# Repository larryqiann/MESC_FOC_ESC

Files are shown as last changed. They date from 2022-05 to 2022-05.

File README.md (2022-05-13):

# MESC_FOC_ESC
MESC, Molony ESC, STM32F303 based FOC+BLDC ready, HALL, Encoder, Sensorless, single sides, 2 layer, ~90A @48V

This ESC is intended as a cost optimised alternative to the VESC, by utilising:

Standalone, industry standard footprint gate drivers

Standard D2PAK or H2PAK FETs

Cheap (~2.5$) STM32F303CB microcontroller

Board dimensions 100mmx50mm, so that it can be panelised and manufactured by JLCPCB, or two boards can be combined into one 100mm2 JLCPCB

It is not cross compatible with VESC software, and does not intend to be. VESC has run away with itself in terms of cost, firmware abstraction... in the opinion of this project's author.

# Current Status:  

## Changes made by larryqiann:
Change power architecture to use MP9486A to create 12V rail, from  which 3.3V and 5V will be regulated to reduce quiescent power draw

Add CAN bus transceiver to support CAN bus integration because F303CB supports CAN2.0b

## Previous:

First build has been made. All functions... function.
Photos in folder! Video of prelim run to be added to Youtube.
Step down works
Step up for Gate drives works
Chip works, all inputs and outputs works
Some concerns about stability of internal opamps... Returning 1.5V instead of 1.6V. First chip soldered returned 1V, and fluctuated by +0.3/-0.1V. 
Motor spins in BLDC mode (6 step) with hall sensors, on Propdrive 2826 1200kV and with APS8072 50kV. Current run up to 20A phase, with minimal PCB heating with no heatsink. Only run to 23V so far, owing to PSU limitation.
FET switching time rather slow with 5 ohm resistors, limiting peak current to 2A (not counting FET and Gate drive resistance) will reduce to 2R7.

# Layout:  
Layout optimised to minimise current loop path, and keep the board completely single sided assembly.

For thermal management, the FETs have vias underneath the drains, which can be interfaced with a heatsink on the PCB underside, using silicone pad/thermal paste & insulator.

# MCU uses:
Timer1 on PA8,9,10 (high) and PB13,14,15 for PWM generation.

Onboard opamps for current sensing and paralelled comparators input on pins PA1,7, PB0.

Phase voltages can be measured on PA3,4,5, or alternatively, digitally read to detect ZC .

Main voltage can be read on PA0.

# Interfaces:
External Interfaces include Hall/Encoder, I2C, PWM in, UART, USB FS.

Hall sensors on Timer4 PB6,7,8, alternatively Encoder can be run on Tim4 PB6,7

Timer3 channel 1 for standard RC PWM input.

USART3 Tx Rx on PB10,11.
USB on PA11,12, with 1k5 pullup to signal FS mode. Canbe used for reflashing (hypothetically).

I2C1 on PA15(SCL) and PB9(SDA), with a plug for a standard SSD1306 breakout. Alternatively, inertial sensor board could be plugged on breakout wire.

Expected BoM cost:  
0.4USD board  
6x2USD FETs  
2.5USD MCU  
3x1USD gate drives  
1USD SMPS converter  
0.4USD inductor  
??? connector cost (dependent on what's fitted, wire in...)  
0.3USD linear reg  
~3USD caps (dependent on how many you want to solder on, which is dependent on distance to battery, desire to comply with EMC, headroom above FET voltage... etc.)  
0.6USD shunts and other resistors  
0.3USD Optional TVS diode, primarily to protect SMPS, which is only rated to 65V  
Total: ~23-24USD

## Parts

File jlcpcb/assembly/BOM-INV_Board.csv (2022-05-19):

Comment | Designator | Footprint | LCSC
AO3401A | Q2 | SOT-23 | C15127
C_10pF | C22,C31 | C_0603_1608Metric | C1634
C_5.1nF | C24,C33 | C_0603_1608Metric | C53987
STM32F303CBTx | U1 | LQFP-48_7x7mm_P0.5mm | C108516
D_Zener_3v3 | D11,D13,D9 | D_MiniMELF | C145245
C_100nF_16V | C25,C37,C5,C8 | C_0603_1608Metric | C14663
C_100pF_16V | C16,C19,C20,C29 | C_0603_1608Metric | C14858
L_47uH_2.0A | L1 | L_Bourns_SRP7028A_7.3x6.6mm | C149588
D_Sch_100V_2A | D14,D4,D8 | D_SOD-123F | C14996
R_82k | R1,R37,R42,R58,R65 | R_0603_1608Metric | C17840
L_15uH_3A | L2,L3 | L_Bourns_SRP7028A_7.3x6.6mm | C182182
INA181 | U4,U6,U7 | SOT-23-6 | C2058943
R_100 | R13,R14 | R_0603_1608Metric | C22775
R_150 | R19,R26,R34 | R_0603_1608Metric | C22808
R_1.5k | R10,R12,R20,R21,R22,R25,R27,R36,R41,R5,R51,R66 | R_0603_1608Metric | C22843
LED_Small | D3 | LED_0603_1608Metric | C2286
R_1.96K | R44 | R_0603_1608Metric | C22975
R_3.24K | R29 | R_0603_1608Metric | C22978
R_30K | R17,R18,R23,R24,R31,R32 | R_0603_1608Metric | C22984
R_4k7 | R11,R15,R2,R30,R33,R4,R6,R7 | R_0603_1608Metric | C23162
R_5 | R38,R39,R40,R45,R46,R47,R48,R49,R50 | R_0603_1608Metric | C23164
R_5.76K | R16,R35 | R_0603_1608Metric | C23189
R_590K | R3 | R_0603_1608Metric | C23203
R_10.2K | R28,R43 | R_0603_1608Metric | C25804
Shunt | R52,R53,R54,R55,R56,R57 | R_2512_6332Metric | C270947
D_Zener_16V | D20,D21,D22,D23,D24,D25 | D_SOD-123 | C27754
C_8.2nF | C21,C30 | C_0603_1608Metric | C27920
C_0.1uF_100V | C1,C10,C17,C4,C52,C68,C7,C71,C9 | C_0603_1608Metric | C28233
IR2181 | U10,U11,U9 | SOIC-8_3.9x4.9mm_P1.27mm | C380794
CRSS037N10N | Q3,Q4,Q5,Q6,Q7,Q8 | TO-263-2 | C455308
C_4.7nF | C11,C12 | C_0603_1608Metric | C53987
D_Sch_100V_2A | D15,D16,D17 | D_SOD-123F | C64898
C_2.2uF 100V | C2,C3 | C_1206_3216Metric | C650969
ASE-xxxMHz | X1 | X1OSC | C70556
C_100uF_25V | C18 | CP_Elec_6.3x7.7 | C72477
D_Zener_3V3 | D19,D26 | D_MiniMELF | C8056
2N7002 | Q1 | SOT-23 | C8545
C_1uF_100V | C34,C35,C36,C38,C39,C40,C47,C48,C50,C51,C53,C54,C55,C56,C57,C58,C59,C6,C60,C61,C62,C64,C67,C69,C70,C72,C73,C74 | C_0603_1608Metric | C91151
Thermistor_NTC | TH1 | R_0603_1608Metric | C92367
C_10uF_25V | C13,C23,C26,C27,C28,C32,C43,C44,C45 | C_0603_1608Metric | C96446
TPS54331DR | U5,U8 | SOIC-8-1EP_3.9x4.9mm_P1.27mm_EP2.29x3mm_ThermalVias | C9865
Conn_01x08_Female | J6 | JST_PH_B8B-PH-K_1x08_P2.00mm_Vertical
SMF05CT1G | U14 | SOT-363_SC-70-6
MP9486A | U3 | SOIC-8-1EP_3.9x4.9mm_P1.27mm_EP2.41x3.3mm_ThermalVias
TJA1051T | U2 | SOIC-8_3.9x4.9mm_P1.27mm
SMF05CT1G | U12 | SOT-363_SC-70-6
SMF05CT1G | U13 | SOT-363_SC-70-6
Conn_01x08_Female | J5 | JST_PH_B8B-PH-K_1x08_P2.00mm_Vertical
CP_470uF+ | C46 | CP_Radial_D16.0mm_P7.50mm
Conn_01x02_Male | J8 | XT60
Conn_01x06_Male | J3 | PinHeader_1x06_P2.54mm_Vertical
Conn_01x06_Female | J4 | JST_PH_B6B-PH-K_1x06_P2.00mm_Vertical
CP_470uF+ | C42 | CP_Radial_D16.0mm_P7.50mm
CP_470uF+ | C41 | CP_Radial_D16.0mm_P7.50mm
Conn_01x05_Male | J7 | JST_PH_B5B-PH-K_1x05_P2.00mm_Vertical

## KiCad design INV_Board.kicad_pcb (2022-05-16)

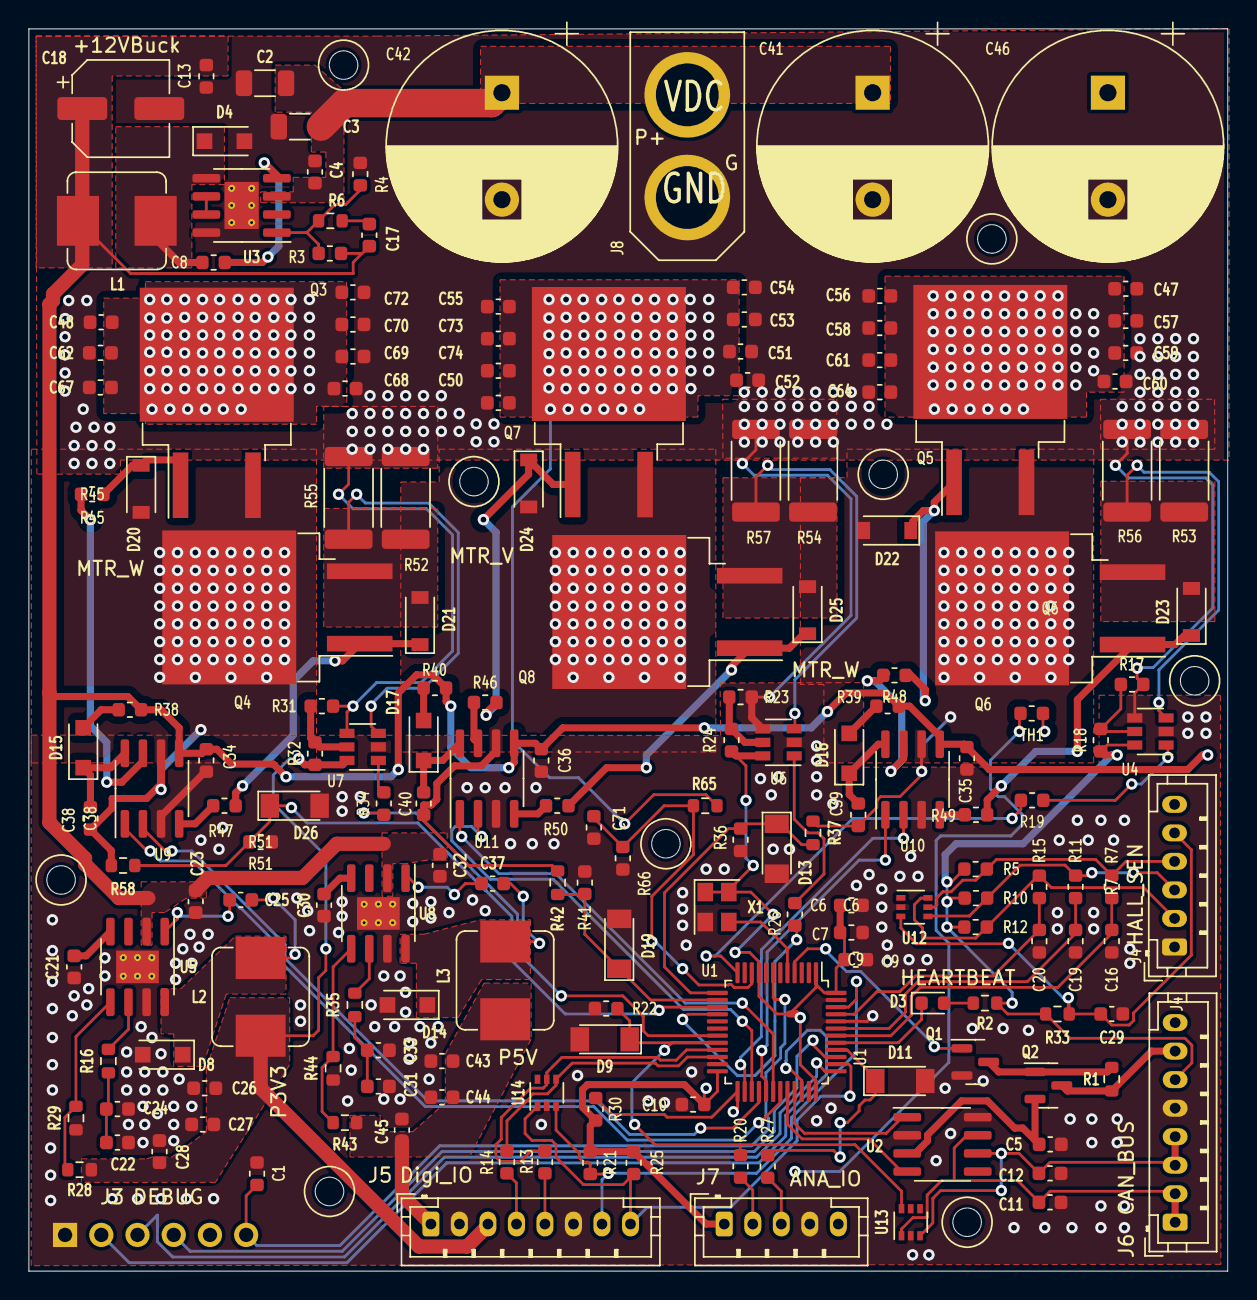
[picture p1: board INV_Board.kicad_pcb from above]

Board: 4 copper layers, 84.1 x 87.1 mm, 177 parts (1 on the bottom side), 97 nets.

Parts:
C1, C4, C7, C9, C10, C17, C52, C68, C71: C_0.1uF_100V; C_0603_1608Metric
C2, C3: C_2.2uF 100V; C_1206_3216Metric
C5, C8, C25, C37: C_100nF_16V; C_0603_1608Metric
C6, C34, C35, C36, C38, C39, C40, C47, C48, C50, C51, C53, C54, C55, C56, C57, C58, C59, C60, C61, C62, C64, C67, C69, C70, C72, C73, C74: C_1uF_100V; C_0603_1608Metric
C11, C12: C_4.7nF; C_0603_1608Metric
C13, C23, C26, C27, C28, C32, C43, C44, C45: C_10uF_25V; C_0603_1608Metric
C16, C19, C20, C29: C_100pF_16V; C_0603_1608Metric
C18: C_100uF_25V; CP_Elec_6.3x7.7
C21, C30: C_8.2nF; C_0603_1608Metric
C22, C31: C_10pF; C_0603_1608Metric
C24, C33: C_5.1nF; C_0603_1608Metric
C41, C42, C46: CP_470uF+; CP_Radial_D16.0mm_P7.50mm
D3: LED_Small; LED_0603_1608Metric
D4, D8, D14, D15, D16, D17: D_Sch_100V_2A; D_SOD-123F
D9, D11, D13: D_Zener_3v3; D_MiniMELF
D19, D26: D_Zener_3V3; D_MiniMELF
D20, D21, D22, D23, D24, D25: D_Zener_16V; D_SOD-123
J3: Conn_01x06_Male; PinHeader_1x06_P2.54mm_Vertical
J4: Conn_01x06_Female; JST_PH_B6B-PH-K_1x06_P2.00mm_Vertical
J5, J6: Conn_01x08_Female; JST_PH_B8B-PH-K_1x08_P2.00mm_Vertical
J7: Conn_01x05_Male; JST_PH_B5B-PH-K_1x05_P2.00mm_Vertical
J8: Conn_01x02_Male; XT60
L1: L_47uH_2.0A; L_Bourns_SRP7028A_7.3x6.6mm
L2, L3: L_15uH_3A; L_Bourns_SRP7028A_7.3x6.6mm
Q1: 2N7002; SOT-23
Q2: AO3401A; SOT-23
Q3, Q4, Q5, Q6, Q7, Q8: CRSS037N10N; TO-263-2
R1, R37, R42, R58, R65: R_82k; R_0603_1608Metric
R2, R4, R6, R7, R11, R15, R30, R33: R_4k7; R_0603_1608Metric
R3: R_590K; R_0603_1608Metric
R5, R10, R12, R20, R21, R22, R25, R27, R36, R41, R51, R66: R_1.5k; R_0603_1608Metric
R13, R14: R_100; R_0603_1608Metric
R16, R35: R_5.76K; R_0603_1608Metric
R17, R18, R23, R24, R31, R32: R_30K; R_0603_1608Metric
R19, R26, R34: R_150; R_0603_1608Metric
R28, R43: R_10.2K; R_0603_1608Metric
R29: R_3.24K; R_0603_1608Metric
R38, R39, R40, R45, R46, R47, R48, R49, R50: R_5; R_0603_1608Metric
R44: R_1.96K; R_0603_1608Metric
R52, R53, R54, R55, R56, R57: Shunt; R_2512_6332Metric
TH1: Thermistor_NTC; R_0603_1608Metric
U1: STM32F303CBTx; LQFP-48_7x7mm_P0.5mm
U2: TJA1051T; SOIC-8_3.9x4.9mm_P1.27mm
U3: MP9486A; SOIC-8-1EP_3.9x4.9mm_P1.27mm_EP2.41x3.3mm_ThermalVias
U4, U6, U7: INA181; SOT-23-6
U5, U8: TPS54331DR; SOIC-8-1EP_3.9x4.9mm_P1.27mm_EP2.29x3mm_ThermalVias
U9, U10, U11: IR2181; SOIC-8_3.9x4.9mm_P1.27mm
U12, U13, U14: SMF05CT1G; SOT-363_SC-70-6
X1: ASE-xxxMHz; X1OSC

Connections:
#RES: C1.1, J3.6, U1.7 (NRST)
+3V3: C6.1, C7.1, C9.1, C10.1, C26.2, C27.2, C28.2, J5.3, J6.6, J7.1, L2.1, R2.1, R5.1, R10.1, R12.1, R18.1, R21.1, R24.1, R25.1, R28.1, R30.1, R32.1, R33.1, U1.1 (VBAT), U1.9 (VDDA), U1.24 (VDD), U1.36 (VDD), U1.48 (VDD), U4.6 (V+), U6.6 (V+), U7.6 (V+), X1.1 (EN), X1.4 (Vdd)
+5V: C43.2, C44.2, C45.2, J4.6, J5.1, J6.7, J7.5, L3.1, Q2.3 (D), R1.1, R43.1
+12V: C13.1, C17.1, C18.1, C23.1, C32.1, C34.1, C35.1, C36.1, J6.8, L1.2, R3.1, R38.1, R39.1, R40.1, U5.2 (VIN), U8.2 (VIN), U9.5 (VCC), U10.5 (VCC), U11.5 (VCC)
+VDC: C2.2, C3.2, C4.1, C41.1, C42.1, C46.1, C47.1, C48.1, C50.1, C51.1, C52.1, C53.1, C54.1, C55.1, C56.1, C57.1, C58.1, C59.1, C60.1, C61.1, C62.1, C64.1, C67.1, C68.1, C69.1, C70.1, C72.1, C73.1, C74.1, J8.2, Q3.2 (D), Q5.2 (D), Q7.2 (D), R65.1, U3.3 (VIN)
/Hall1: C16.1, R7.1, U1.42 (PB6)
/Hall2: C19.1, R11.1, U1.43 (PB7)
/Hall3: C20.1, R15.1, U1.45 (PB8)
/UGH: D22.1 (K), Q5.1 (G), R48.2
/UGL: D23.1 (K), Q6.1 (G), R49.2
/VGH: D24.1 (K), Q7.1 (G), R46.2
/VGL: D25.1 (K), Q8.1 (G), R50.2
/WGH: D20.1 (K), Q3.1 (G), R45.2
/WGL: D21.1 (K), Q4.1 (G), R47.2
/op1Vout: R19.1, U1.12 (PA2)
/op2Vout: R26.1, U1.16 (PA6)
/op3Vout: R34.1, U1.19 (PB1)
AnalogIn: D9.1 (K), R20.1, R22.1, U1.20 (PB2), U13.6 (K)
BoardTemp: R30.2, TH1.1, U1.25 (PB12)
CAN_EN: Q1.1 (G), U1.4 (PC15)
CAN_RXD: U1.32 (PA11), U2.4 (RXD)
CAN_TXD: U1.33 (PA12), U2.1 (TXD)
HeartBeat_LED: D3.1 (K), U1.41 (PB5)
I2CSCL: J5.8, R25.2, U1.38 (PA15), U14.1 (K)
I2CSDA: J5.7, R21.2, U1.46 (PB9), U14.3 (K)
ISU: D23.2 (A), Q6.3 (S), R53.1, R56.1, U4.3 (+)
ISV: D25.2 (A), Q8.3 (S), R54.1, R57.1, U6.3 (+)
ISW: D21.2 (A), Q4.3 (S), R52.1, R55.1, U7.3 (+)
Motor_T: C29.1, J4.5, R33.2, U12.3 (K)
unnamed: C5.1, Q2.2 (S), U2.3 (VCC)
unnamed: C8.1, U3.4 (BST)
unnamed: C8.2, D4.1 (K), L1.1, U3.5 (SW)
unnamed: C11.2, J6.1, J6.2, U2.7 (CANH), U13.1 (K)
unnamed: C12.2, J6.3, J6.4, U2.6 (CANL), U13.3 (K)
unnamed: C17.2, R6.2
unnamed: C21.1, U5.4 (SS)
unnamed: C22.1, C24.1, R16.2
unnamed: C25.1, U5.1 (BOOT)
unnamed: C25.2, D8.1 (K), L2.2, U5.8 (PH)
unnamed: C30.1, U8.4 (SS)
unnamed: C31.1, C33.1, R35.2
unnamed: C37.1, U8.1 (BOOT)
unnamed: C37.2, D14.1 (K), L3.2, U8.8 (PH)
unnamed: C38.1, D15.1 (K), U9.8 (VB)
unnamed: C39.1, D16.1 (K), U10.8 (VB)
unnamed: C40.1, D17.1 (K), U11.8 (VB)
unnamed: D3.2 (A), R2.2
unnamed: D15.2 (A), R38.2
unnamed: D16.2 (A), R39.2
unnamed: D17.2 (A), R40.2
unnamed: J4.2, R12.2, R15.2, U12.6 (K)
unnamed: J4.3, R10.2, R11.2, U12.4 (K)
unnamed: J4.4, R5.2, R7.2, U12.5 (K)
unnamed: J5.4, R14.1
unnamed: J5.5, R13.2
unnamed: J7.2, R20.2
unnamed: J7.3, R27.2
unnamed: Q1.3 (D), Q2.1 (G), R1.2
unnamed: R3.2, R4.1, R6.1, U3.1 (FB)
unnamed: R16.1, U5.6 (COMP)
unnamed: R17.1, R18.2, U4.5 (REF)
unnamed: R19.2, U4.1
unnamed: R23.1, R24.2, U6.5 (REF)
unnamed: R26.2, U6.1
unnamed: R28.2, R29.1, U5.5 (VSENSE)
unnamed: R31.1, R32.2, U7.5 (REF)
unnamed: R34.2, U7.1
unnamed: R35.1, U8.6 (COMP)
unnamed: R43.2, R44.1, U8.5 (VSENSE)
unnamed: R45.1, U9.7 (HO)
unnamed: R46.1, U11.7 (HO)
unnamed: R47.1, U9.4 (LO)
unnamed: R48.1, U10.7 (HO)
unnamed: R49.1, U10.4 (LO)
unnamed: R50.1, U11.4 (LO)
unnamed: U1.5 (PF0), X1.3 (OUT)
unnamed: U3.6 (DIM), U3.7 (EN)
PWMin: D11.1 (K), R27.1, U1.40 (PB4)
PhaseU: D13.1 (K), R36.1, R37.2, U1.13 (PA3)
PhaseV: D19.1 (K), R41.1, R42.2, U1.14 (PA4)
PhaseW: D26.1 (K), R51.1, R58.2, U1.15 (PA5)
SGU: C1.2, C2.1, C3.1, C4.2, C5.2, C6.2, C7.2, C9.2, C10.2, C11.1, C12.1, C13.2, C16.2, C18.2, C19.2, C20.2, C21.2, C22.2, C23.2, C24.2, C26.1, C27.1, C28.1, C29.2, C30.2, C31.2, C32.2, C33.2, C34.2, C35.2, C36.2, C41.2, C42.2, C43.1, C44.1, C45.1, C46.2, C47.2, C48.2, C50.2, C51.2, C52.2, C53.2, C54.2, C55.2, C56.2, C57.2, C58.2, C59.2, C60.2, C61.2, C62.2, C64.2, C67.2, C68.2, C69.2, C70.2, C71.2, C72.2, C73.2, C74.2, D4.2 (A), D8.2 (A), D9.2 (A), D11.2 (A), D13.2 (A), D14.2 (A), D19.2 (A), D26.2 (A), J3.1, J4.1, J5.2, J5.6, J6.5, J7.4, J8.1, Q1.2 (S), R4.2, R17.2, R22.2, R23.2, R29.2, R31.2, R36.2, R41.2, R44.2, R51.2, R52.2, R53.2, R54.2, R55.2, R56.2, R57.2, R66.2, TH1.2, U1.8 (VSSA), U1.23 (VSS), U1.35 (VSS), U1.44 (BOOT0), U1.47 (VSS), U2.2 (GND), U2.8 (S), U3.8 (GND), U3.9 (EP), U4.2 (GND), U4.4 (-), U5.7 (GND), U5.9 (EP), U6.2 (GND), U6.4 (-), U7.2 (GND), U7.4 (-), U8.7 (GND), U8.9 (EP), U9.3 (COM), U10.3 (COM), U11.3 (COM), U12.2 (A), U13.2 (A), U14.2 (A), X1.2 (GND)
STRx: R14.2, U1.22 (PB11), U14.4 (K)
STTx: R13.1, U1.21 (PB10), U14.5 (K)
SWCLK: J3.3, U1.37 (PA14)
SWDIO: J3.2, U1.34 (PA13)
SWO: J3.4, U1.39 (PB3)
SWU: C39.2, D22.2 (A), Q5.3 (S), Q6.2 (D), R37.1, U10.6 (VS)
SWV: C40.2, D24.2 (A), Q7.3 (S), Q8.2 (D), R42.1, U11.6 (VS)
SWW: C38.2, D20.2 (A), Q3.3 (S), Q4.2 (D), R58.1, U9.6 (VS)
UHin: U1.29 (PA8), U10.1 (HIN)
ULin: U1.26 (PB13), U10.2 (LIN)
VHin: U1.30 (PA9), U11.1 (HIN)
VLin: U1.27 (PB14), U11.2 (LIN)
Vsense_MCU: C71.1, R65.2, R66.1, U1.10 (PA0)
WHin: U1.31 (PA10), U9.1 (HIN)
WLin: U1.28 (PB15), U9.2 (LIN)

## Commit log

2022-05-13 Schematic Changes (Incomplete)
    [INV_Board.kicad_sch]
2022-05-14 Checkpoint before deleting MCU ISense
    [INV_Board.kicad_sch]
2022-05-15 Save progress
    [INV_Board.kicad_pcb]
2022-05-16 Update progress
    [INV_Board.kicad_pcb, INV_Board.kicad_sch]
2022-05-19 00A revision as ordered
    00A version of board has been ordered for assembly. Warning: this commit contains some fixes which were not part of the order
    [BOM-INV_Board.csv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]
